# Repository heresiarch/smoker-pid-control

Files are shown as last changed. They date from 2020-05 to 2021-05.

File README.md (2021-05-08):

# smoker-pid-control
Arduino based PID Controller with PT1000 elements to control heat in BBQ grill using a blower fan
* PWM Output 0-255 
* Manual controller mode
* PID based controller mode
* Fuzzy based controller mode
* OLED Display
* Adafruit MAX31865 RTD Sensor Breakout module
* Arduino Micro
* Rotary Encoder user interface

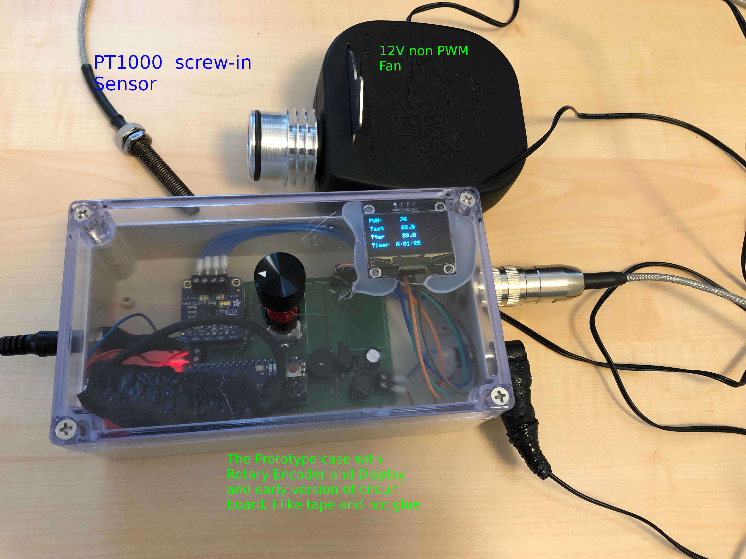
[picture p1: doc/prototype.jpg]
Logo Title Text 1


# Field Test
## PID Mode
PID Mode works very well with Weber 57 cm BBQ Grill. Only small overshots in the beginning. I use a BBQ Guru Viper Pit 12 V Fan which has no PWM, PWM is converted to linear voltage with a simple Buck converter. PID Values are very much dependend on the type of BBQ Grill. I have a hard cut off rule above 1.0 °C which counters some overshots in the beginning. Autotune experiments are a good waste of time IMHO, better is to use PID values based on experiments. 

## Fuzzy Mode
Fuzzy mode is very stable and gets good steady state for setpoint temperature. Fuzzy mode is controlled by Fuzzyset based on temperature difference. You should change rules sets based on your setup and used MOSFET (RDSon and PWM values). Fuzzy update rate is 5 seconds. I derived a simple fuzzy set from the much more sophisticated example from the link below, which has unfortunately too many rules for my Arduino Micro memory: https://github.com/rvt/bbq-controller/blob/master/lib/bbq/bbqfanonly.cpp.

## Results
Overall I could hold constant temperature of 110 °C over 4 hours with 1 char basket filled with some weber charcoal briquettes, and still had enough of them left for some hours. With 2 char baskets starting on each side with 2-3 hot coals in ignition cord style and with grill fully meat loaded I got superior results in temperature stability with the Fuzzy Sets defined.

## References and similar Projects
* [Smokerduino on Instructables](https://www.instructables.com/id/Smokerduino/)
* [Fuzzy based BBQ Controler Project](https://github.com/rvt/bbq-controller)
* [Small OLED Library ss_oled](https://github.com/bitbank2/ss_oled)
* [Another small OLED Library SSD1306Ascii](https://github.com/greiman/SSD1306Ascii)

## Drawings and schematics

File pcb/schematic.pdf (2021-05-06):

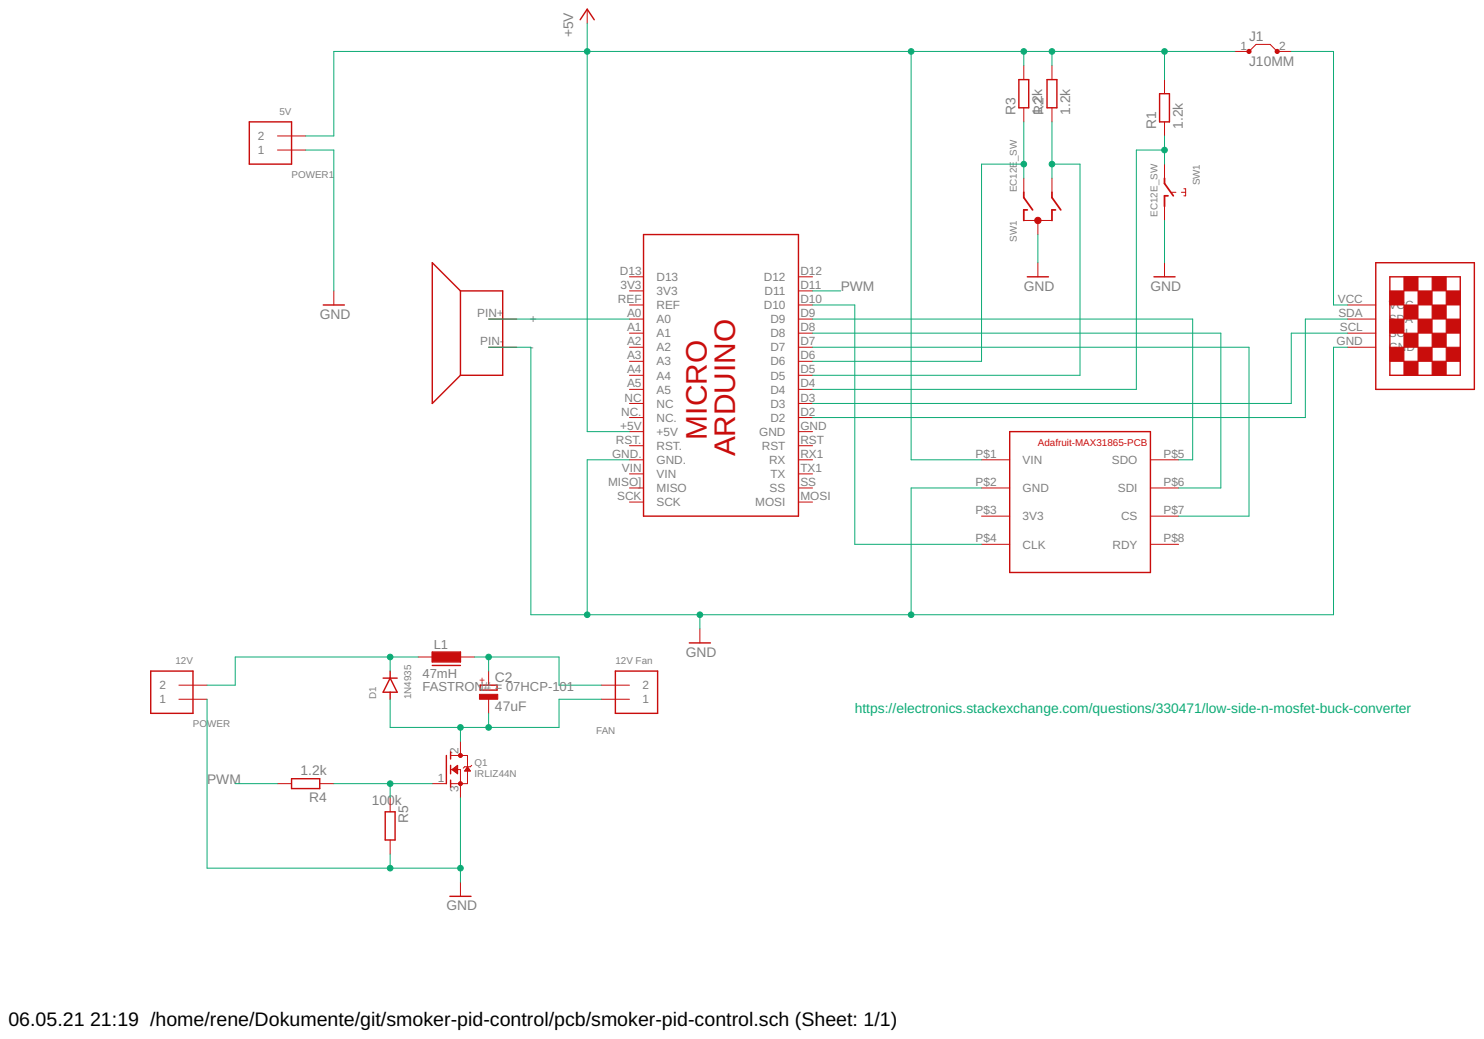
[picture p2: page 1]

https://electronics.stackexchange.com/questions/330471/low-side-n-mosfet-buck-converter FASTRON# = 07HCP-101

06.05.21 21:19 /home/rene/Dokumente/git/smoker-pid-control/pcb/smoker-pid-control.sch (Sheet: 1/1)

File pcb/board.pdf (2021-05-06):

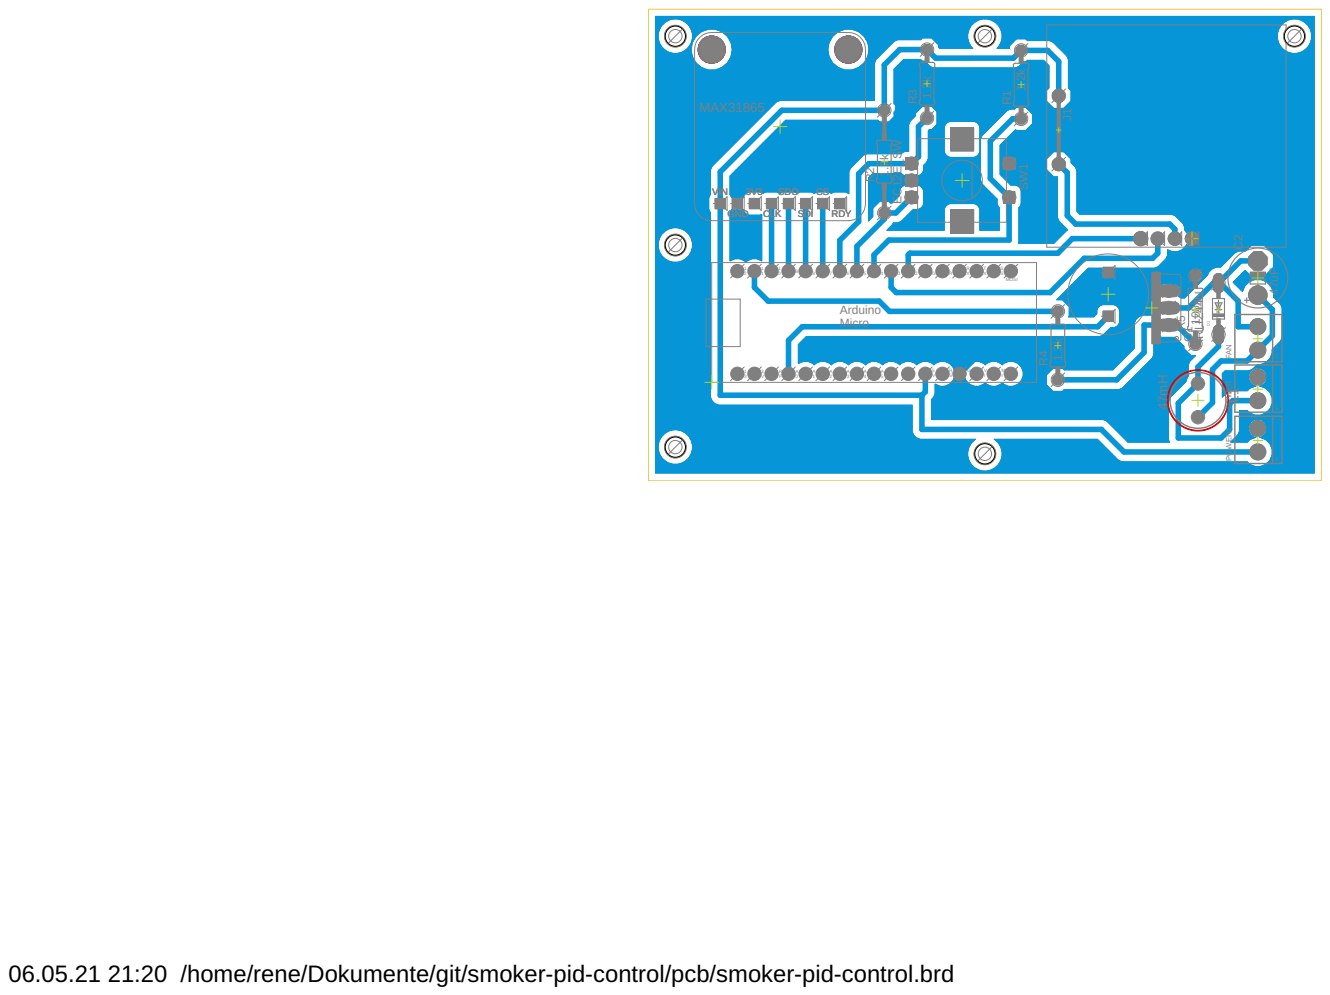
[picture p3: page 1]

06.05.21 21:20 /home/rene/Dokumente/git/smoker-pid-control/pcb/smoker-pid-control.brd

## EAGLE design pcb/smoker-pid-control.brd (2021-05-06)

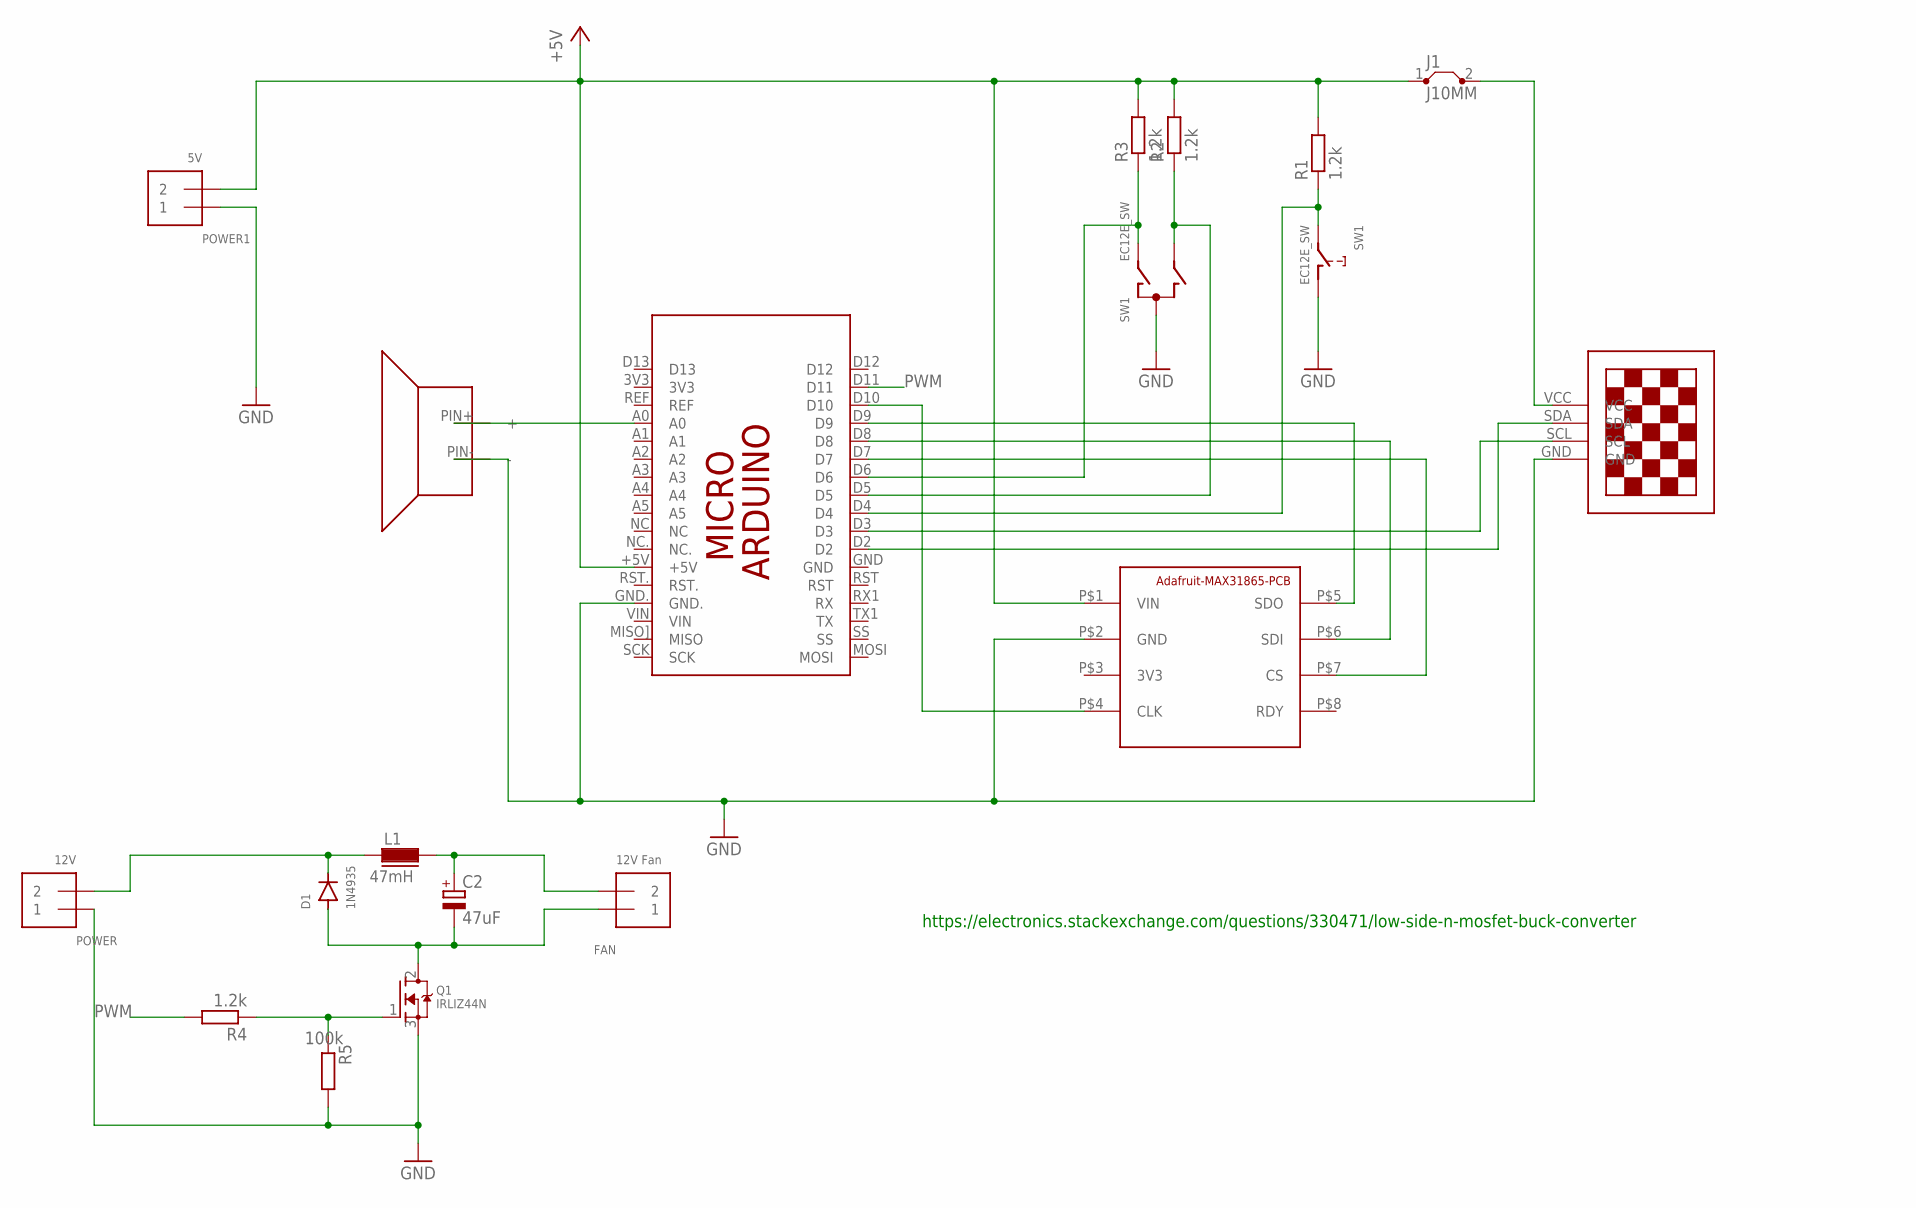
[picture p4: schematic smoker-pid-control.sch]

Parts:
C2: 47uF; E5-8,5
D1: 1N4935; DO34-7
FAN: 12V Fan; TERMBLOCK_1X2-3.5MM
J1: J10MM; 10
L1: 47mH; FASTRON_07HCP_INDUCTOR
PCB1: ARDUINO_MICRO
POWER: 12V; TERMBLOCK_1X2-3.5MM
POWER1: 5V; TERMBLOCK_1X2-3.5MM
Q1: IRLIZ44N; TO220V
R1, R3, R4: 1.2k; 0207/10
R2: 1.2k; 0207/15
R5: 100k; 0207/10
SW1: EC12E_SW; ALPS_EC12E_SW
U$1: ADAFRUIT-MAX31865; MAX31865-BRD
U$2: 13"OLED13"OLED; 1.3"OLED
U$3: KC-1206

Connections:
3V3: U$1.P$3 (3V3)
+5V: J1.1, PCB1.+5V, POWER1.2, R1.2, R2.2, R3.2, U$1.P$1 (VIN)
GND: PCB1.GND., POWER.1, POWER1.1, Q1.3 (S), R5.2, SW1.C, SW1.D (1), U$1.P$2 (GND), U$2.GND, U$3.PIN- (-)
unnamed: PCB1.D2, U$2.SDA
unnamed: PCB1.D3, U$2.SCL
unnamed: PCB1.D10, U$1.P$4 (CLK)
unnamed: PCB1.D4, R1.1, SW1.E (2)
unnamed: PCB1.D9, U$1.P$5 (SDO)
unnamed: PCB1.D8, U$1.P$6 (SDI)
unnamed: PCB1.D7, U$1.P$7 (CS)
unnamed: PCB1.D5, R2.1, SW1.B
unnamed: PCB1.D6, R3.1, SW1.A
unnamed: PCB1.A0, U$3.PIN+ (+)
unnamed: C2.+, FAN.2, L1.2
unnamed: Q1.1 (G), R4.1, R5.1
unnamed: J1.2, U$2.VCC
unnamed: C2.-, D1.A, FAN.1, Q1.2 (D)
unnamed: D1.C, L1.1, POWER.2
PWM: PCB1.D11, R4.2

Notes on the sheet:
https://electronics.stackexchange.com/questions/330471/low-side-n-mosfet-buck-converter

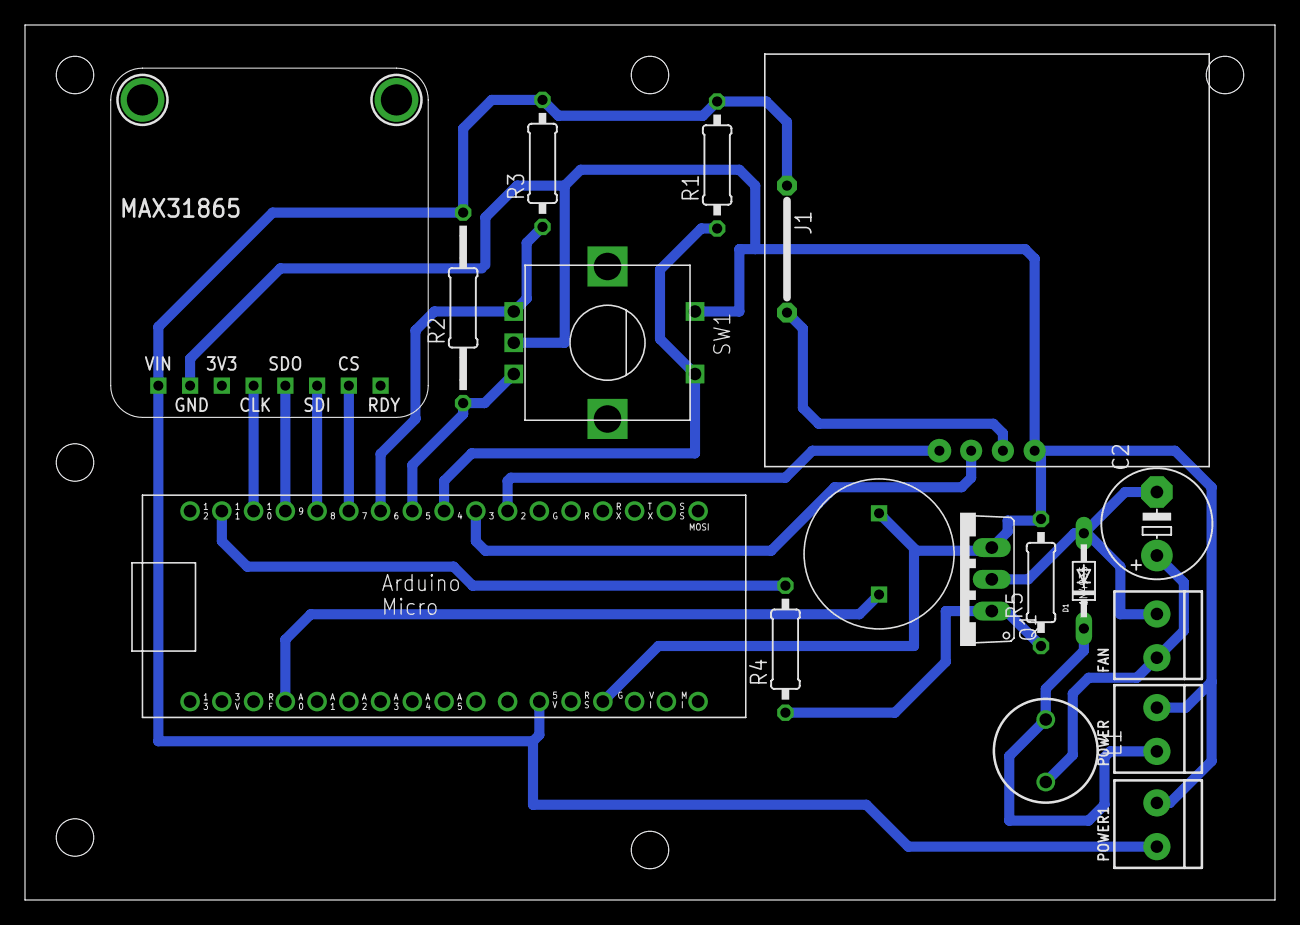
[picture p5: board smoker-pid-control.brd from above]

Board: 2 copper layers, 100.0 x 70.0 mm, 18 parts (0 on the bottom side), 18 nets.

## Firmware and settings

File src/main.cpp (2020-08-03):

#include <Arduino.h>
#include <avr/pgmspace.h>

#include <Adafruit_MAX31865.h>
#include <TimerFour.h>
#include <PID_v1.h>

#include <Wire.h>
#include "SSD1306Ascii.h"
#include "SSD1306AsciiWire.h"

#include "MyButton.h"
#include "RotaryEncoderSwitch.h"
#include "PlatinumSensor.h"
#include "bbqfan.h"

int pwmPin = 11;

#define OLED_ADDR 0x3C

//SSOLED ssoled;
SSD1306AsciiWire oled;

Adafruit_MAX31865 max = Adafruit_MAX31865(7, 8, 9, 10);
RotaryEnoderSwitch rot = RotaryEnoderSwitch(6, 5, EncoderType::twoStep);
MyButton mybutton = MyButton(4, true, false);

enum operatingState
{
  INIT = 0,
  OFF,
  SET_TEMP,
  SET_TIMER,
  MENU,
  MANUAL_MODE,
  RUN_FUZZY,
  PREP_PID,
  RUN_PID,
  AUTO_TIMER,
  FINISH
};
operatingState opState = OFF;
operatingState history = OFF;

#define RIGHT_MOVE 0
#define LEFT_MOVE 1
#define BUTTON_PUSH 2
#define BUTTON_LONG_PUSH 3

uint16_t startMillis; //some global variables available anywhere in the program
uint16_t currentMillis;
uint16_t period = 1000; //the value is a number of milliseconds

double currentTemp = 0.0;
double targetTemp = 60.0;
#define TARGET_TEMP_MAX 180.0
#define TARGET_TEMP_MIN 20.0
#define TIMER_MAX 840
#define TIMER_MIN 5
uint32_t targetTimer = TIMER_MIN;
uint32_t countDown = 0;
uint32_t lastTime = 0;

uint8_t pwmValue = 0;
#define MAX_PWM 255
#define MIN_PWM 17

double outputVal;
double aggKp = 8, aggKi = 0.2, aggKd = 1;
double consKp = 2, consKi = 0.05, consKd = 0.25;

PID myPID(&currentTemp, &outputVal, &targetTemp, consKp, consKi, consKd, DIRECT);
BBQFan bbqfan(currentTemp, targetTemp, pwmValue);
unsigned long lastFuzzy = 0;
#define FUZZY_PERIOD_MS 5000

const char s_00[] = "BBQ is Off    \0";
const char s_01[] = "Press Button  \0";
const char s_02[] = "Set Temp in  C\0";
const char s_03[] = "Set Timer min \0";
const char s_04[] = " Manual Mode  \0";
const char s_05[] = " PID Control  \0";
const char s_06[] = " Fuzzy        \0";
const char s_07[] = " Reset        \0";
const char s_08[] = "PWM:           \0";
const char s_09[] = "Tact           \0";
const char s_10[] = "Ttar           \0";
const char s_11[] = "Timer          \0";
const char s_12[] = "               \0";
const char s_13[] = "**** Ready ****\0";
const char s_14[] = "** Enjoy it! **\0";
const char *const string_table[] = {s_00, s_01, s_02, s_03, s_04, s_05, s_06, s_07, s_08, s_09, s_10, s_11, s_12, s_13, s_14};

uint8_t menuIdx = 0;

char buffer[30];
char *fillBuffer(int i)
{
  memset(buffer, 0, sizeof(buffer));
  strcpy(buffer, string_table[i]);
  return buffer;
}

void timer4(void)
{
  rot.tickDebounceDecode();
  mybutton.debounce();
}

void setup()
{
  // PWM on Pin 3
  //http://www.scynd.de/tutorials/arduino-tutorials/3-luefter-steuern/3-1-pwm-ohne-pfeifen.html
  //TCCR1B = TCCR1B & 0b11111000 | 0x01;
  pinMode(pwmPin, OUTPUT);
  max.begin(MAX31865_4WIRE);
  Timer4.initialize(1000);
  Timer4.attachInterrupt(timer4);
  opState = INIT;
  Wire.begin();
  Wire.setClock(400000L);
  oled.begin(&SH1106_128x64, OLED_ADDR);
  oled.setFont(Adafruit5x7);
  oled.clear();
}

float readTemperature(void)
{
  float rtd = (float)max.readRTD();
  float ratio = rtd;
  ratio /= 32768;
  // Check and print any faults
  float temp = PlatinumSensor::tempFromPtResistance(4300.00 * ratio, 1000.00);
  uint8_t fault = max.readFault();
  if (fault)
  {
    max.clearFault();
  }
  return temp;
}

uint8_t readButtons()
{
  uint8_t buttons = 0;
  int8_t idx = rot.readEncoder();
  if (idx > 0)
    buttons |= (1 << LEFT_MOVE);
  else if (idx < 0)
    buttons |= (1 << RIGHT_MOVE);

  currentMillis = millis();
  if (mybutton.buttonPressed() && (currentMillis - startMillis >= period))
  {
    startMillis = currentMillis;
    if (mybutton.longPressed())
      buttons |= (1 << BUTTON_LONG_PUSH);
    else
      buttons |= (1 << BUTTON_PUSH);
  }
  return buttons;
}

void welcomeMsg(void)
{
  oled.setCursor(0, 0);
  oled.println(fillBuffer(0));
  oled.println(fillBuffer(1));
}

void targetTempMsg(void)
{
  oled.setCursor(0, 0);
  oled.println(fillBuffer(2));
  oled.setCursor(0, 3);
  oled.print(targetTemp, 0);
}

void timerMsg(void)
{
  oled.setCursor(0, 0);
  oled.println(fillBuffer(3));
  uint8_t hours = targetTimer / 60;
  uint8_t minutes = targetTimer % 60;
  countDown = targetTimer * 60;
  dtostrf(hours, 2, 0, &buffer[0]);
  buffer[2] = ':';
  dtostrf(minutes, 2, 0, &buffer[3]);
  if (minutes < 10)
    buffer[3] = '0';
  oled.setCursor(0, 3);
  oled.println(buffer);
}

void menuMsg()
{ //TODO rework scrolling too many ifs
  oled.setCursor(0, 0);
  for (uint8_t i = 0; i < 4; i++)
  {
    fillBuffer(4 + i);
    if (i == menuIdx)
    {
      buffer[0] = '*';
    }
    oled.println(buffer);
  }
}

void manualMsg()
{
  oled.setCursor(0, 0);

  fillBuffer(8);
  dtostrf(pwmValue, 3, 0, &buffer[8]);
  oled.println(buffer);
  oled.println();

  fillBuffer(9);
  dtostrf(currentTemp, 6, 1, &buffer[7]);
  oled.println(buffer);
  oled.println();

  fillBuffer(10);
  dtostrf(targetTemp, 6, 1, &buffer[7]);
  oled.println(buffer);
  oled.println();

  fillBuffer(11);
  uint8_t hours = (countDown / 3600);
  uint8_t minutes = (countDown - (3600 * hours)) / 60;
  uint8_t seconds = (countDown - (3600 * hours) - (minutes * 60));
  dtostrf(hours, 2, 0, &buffer[6 + 0]);
  buffer[6 + 2] = ':';
  dtostrf(minutes, 2, 0, &buffer[6 + 3]);
  if (minutes < 10)
    buffer[6 + 3] = '0';
  buffer[6 + 5] = ':';
  dtostrf(seconds, 2, 0, &buffer[6 + 6]);
  if (seconds < 10)
    buffer[6 + 6] = '0';
  oled.println(buffer);
}

void finishMsg(void)
{

  oled.setInvertMode(true);
  oled.setCursor(0, 0);
  oled.println(fillBuffer(13));
  oled.println(fillBuffer(14));
}

void doControll(void)
{
  if (opState == RUN_PID)
  {
    double gap = targetTemp - currentTemp;
    if (gap <= -1.0)
    {
      pwmValue = 0;
    }
    else if (gap > 0 && gap <= 10)
    { //we're close to setpoint, use conservative tuning parameters
      myPID.SetTunings(consKp, consKi, consKd);
      myPID.Compute();
      pwmValue = map(outputVal, 0, 255, MIN_PWM, 255);
      if (pwmValue > MAX_PWM)
      {
        pwmValue = MAX_PWM;
      }
    }
    else
    { //we're far from setpoint, use aggressive tuning parameters
      myPID.SetTunings(aggKp, aggKi, aggKd);
      myPID.Compute();
      pwmValue = map(outputVal, 0, 255, MIN_PWM, 255);
      if (pwmValue > MAX_PWM)
      {
        pwmValue = MAX_PWM;
      }
    }
  }
  else if (opState == RUN_FUZZY)
  {
    if (millis() - lastFuzzy >= FUZZY_PERIOD_MS)
    {
      lastFuzzy = millis(); //get ready for the next iteration
      bbqfan.handle();
    }
  }
}

void loop()
{
  // always read temperature
  currentTemp = readTemperature();
  uint8_t buttons = readButtons();
  if (buttons & (1 << BUTTON_LONG_PUSH))
  {
    opState = INIT;
  }
  switch (opState)
  {
  case INIT:
    opState = OFF;
    pwmValue = 0;
    outputVal = 0.0;
    oled.setInvertMode(false);
    oled.clear();
    break;
  case OFF:
    welcomeMsg();
    if (buttons & (1 << BUTTON_PUSH))
    {
      opState = SET_TEMP;
      oled.clear();
    }
    pwmValue = 0;
    break;

  case SET_TEMP:
    targetTempMsg();
    if (buttons & (1 << LEFT_MOVE) && targetTemp < TARGET_TEMP_MAX)
    {
      targetTemp += 1.0;
    }
    else if (buttons & (1 << RIGHT_MOVE) && targetTemp > TARGET_TEMP_MIN)
    {
      targetTemp -= 1.0;
    }
    if (buttons & (1 << BUTTON_PUSH))
    {
      opState = SET_TIMER;
      oled.clear();
    }
    break;

  case SET_TIMER:
    timerMsg();
    if (buttons & (1 << LEFT_MOVE) && targetTimer < TIMER_MAX)
    {
      targetTimer += 5;
    }
    else if (buttons & (1 << RIGHT_MOVE) && targetTimer > TIMER_MIN)
    {
      targetTimer -= 5;
    }
    if (buttons & (1 << BUTTON_PUSH))
    {
      opState = MENU;
    }
    break;
    countDown = targetTimer * 60000;

  case MENU:
    menuMsg();
    if (buttons & (1 << LEFT_MOVE) && menuIdx < 3)
    {
      menuIdx++;
    }
    else if (buttons & (1 << RIGHT_MOVE) && menuIdx > 0)
    {
      menuIdx--;
    }
    if (buttons & (1 << BUTTON_PUSH))
    {
      if (menuIdx == 0)
        opState = MANUAL_MODE;
      else if (menuIdx == 1)
        opState = PREP_PID;
      else if (menuIdx == 2)
        opState = RUN_FUZZY;
      else
        opState = INIT;
      oled.clear();
    }
    break;

  case MANUAL_MODE:
    manualMsg();
    if (buttons & (1 << LEFT_MOVE) && pwmValue < MAX_PWM)
    {
      pwmValue++;
    }
    else if (buttons & (1 << RIGHT_MOVE) && pwmValue > 0)
    {
      pwmValue--;
    }
    history = opState;
    opState = AUTO_TIMER;
    break;
  case RUN_FUZZY:
    manualMsg();
    doControll();
    history = opState;
    opState = AUTO_TIMER;
    break;
  case PREP_PID:
    myPID.SetMode(MANUAL);
    outputVal = 0.0;
    myPID.SetMode(AUTOMATIC);
    opState = RUN_PID;
    break;
  case RUN_PID:
    manualMsg();
    doControll();
    history = opState;
    opState = AUTO_TIMER;
    break;
  case AUTO_TIMER:
    opState = history;
    if (millis() - lastTime >= 1000)
    {
      lastTime = millis();
      countDown -= 1;
    }
    if (countDown == 0)
    {
      oled.clear();
      opState = FINISH;
      pwmValue = 0;
    }
    break;
  case FINISH:
    finishMsg();
    tone(18, 2400, 250);
    delay(1000);
    break;
  default:
    opState = INIT;
    break;
  }
  analogWrite(pwmPin, pwmValue);
}

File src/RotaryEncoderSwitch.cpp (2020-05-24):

#include "Arduino.h"
#include "RotaryEncoderSwitch.h"


RotaryEnoderSwitch::RotaryEnoderSwitch(uint8_t pinA, uint8_t pinB,EncoderType type)
{
    this->pinA = pinA;
    this->pinB = pinB;
    this->type = type;
    // enable input pins
    pinMode(this->pinA,INPUT);
    pinMode(this->pinB,INPUT);
    
    int8_t newval = 0;
    if( digitalRead(this->pinA) )
        newval = 3;
    if( digitalRead(this->pinB) )
        newval ^= 1;                   // convert gray to binary
    last_val = newval;                   // power on state
    enc_delta = 0;
}

void RotaryEnoderSwitch::tickDebounceDecode(void){
  int8_t new_val, diff;
  new_val = 0;
  if( digitalRead(this->pinA) )
    new_val = 3;
  if( digitalRead(this->pinB) )
    new_val ^= 1;                   // convert gray to binary
  diff = last_val - new_val;                // difference last - new
  if( diff & 1 ){               // bit 0 = value (1)
    last_val = new_val;                 // store new as next last
    enc_delta += (diff & 2) - 1;        // bit 1 = direction (+/-)
  }   
}

int8_t RotaryEnoderSwitch::readEncoder(void)
{
    int8_t ret = 0;
    switch(type)
    {
        case EncoderType::singleStep:
            ret = encode_read1();
            break;
        case EncoderType::twoStep:
            ret = encode_read2();
            break;
        case EncoderType::fourStep:
            ret = encode_read4();
            break;
        default:
            break;         
    }
    return ret;
}

int8_t RotaryEnoderSwitch::encode_read1( void )         // read single step encoders
{
  int8_t val;
  val = enc_delta;
  enc_delta = 0;
  return val;                   // counts since last call
}

int8_t RotaryEnoderSwitch::encode_read2( void )         // read two step encoders
{
  int8_t val;
  val = enc_delta;
  enc_delta = val & 1;
  return val >> 1;
}

int8_t RotaryEnoderSwitch::encode_read4( void )         // read four step encoders
{
  int8_t val;
  val = enc_delta;
  enc_delta = val & 3;
  return val >> 2;
}

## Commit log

2020-06-26 display PWM in manual mode if changed
2020-06-28 PID Control added
2020-06-29 new PID
2020-06-29 better PID Control
2020-06-29 new delete is not good in arduino
2020-08-02 simplify fuzzy init, avoid multiples new delete
    [bbqfan.cpp, main.cpp]
2020-08-03 pwm limits
2021-04-11 eagle pcb
2021-04-11 eagle 2
    [pcb.kicad_pcb, pcb.sch, smoker-pid-control.brd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]
2021-04-17 pcb with pulldown on gate
    [smoker-pid-control.brd, smoker-pid-control.sch]
2021-04-24 fix drill hole sizes, fix oled wiring bug
    [smoker-pid-control.brd, smoker-pid-control.sch]
2021-04-26 single layer Layout, groundplane fix, stronger airwires
    [smoker-pid-control.brd, smoker-pid-control.sch]
2021-05-01 final pcb
    [smoker-pid-control.brd, smoker-pid-control.sch]
2021-05-04 optimise space
    [smoker-pid-control.brd]
2021-05-06 fix Micro power path from Vin to 5V pin, separate 5V and 12V supply
    [smoker-pid-control.brd, smoker-pid-control.sch]
2021-05-08 final prototype ready
